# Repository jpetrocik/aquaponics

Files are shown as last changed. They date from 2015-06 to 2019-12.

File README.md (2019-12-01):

# Aquaponic's Firmware For Sonoff Dual R2

Firmware to control an aquaponics system using Sonoff Dual R2.  The Sonoff Dual R2 has two relays to control the pumps, the firmware acts as a timer to control the rely and provides a RestApi to control the pumps from OpenHab or HomeAssistant. The Sonoff curcuit board is removed from the orginal Sonoff enclosure and put into a weather proof enclosure ordered from Amazon.

### Sonoff Dual R2

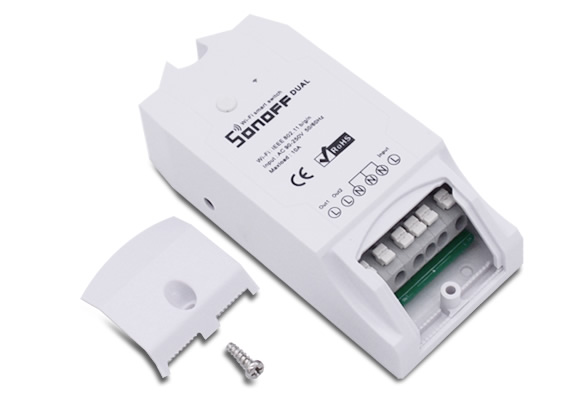
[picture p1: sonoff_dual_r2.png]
Dual R2


## Flashing Firmware

The Sonoff uses a ESP8266 Wifi chip, so this section discusses flashing the ESP8266 chip on the Sonoff Dual R2. For more details google: "Arduino ESP8266"

### Setup the Arduino IDE

* Download Arduino IDE.

* Open you IDE and click on "File -> Preferences".

* In  "Aditional Boards Manager URLs" add this line and click on "OK": "http://arduino.esp8266.com/stable/package_esp8266com_index.json"

* Go to "Tools -> Board -> Boards Manager", type "ESP8266" and install it.

* Go again to "Tools -> Board" and select "Generic ESP8266 Module".

### Flashing

* Place a jumper on the pins labeled BUTTON 0 and GND, without this the Sonoff does not enter flash mode.

* Connect the TTL programmer to programming header pins on the Sonoff.  You must cross over the RX->TX and TX-RX.  So from the promgrammer connect TX -> RX on the Sonoff and RX to TX on the Sonoff.  Connect 3.3v and GND.

* Plug in the programmer your computer.

* Using Adruino IDE, open "firmware.ino" from this project.

* From the menu: Tool -> Boards -> "Generic ESP8266 Module"

* After selecting the board change the following defaults from the Tool menu:

Flash Mode: DOUT (compatiable)

Flash Size: 1M (no spiff)

Port: \<select your programmer from the list\>

* Programming the Sonoff by clickign to "Upload" icon

## Sonoff Dual R2 Programming Headers 

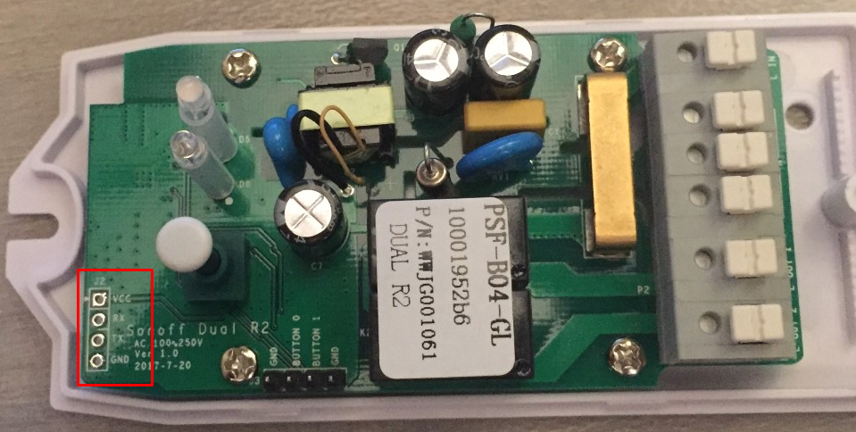
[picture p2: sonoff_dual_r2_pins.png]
Dual R2 Programming Headers


## Enclosure

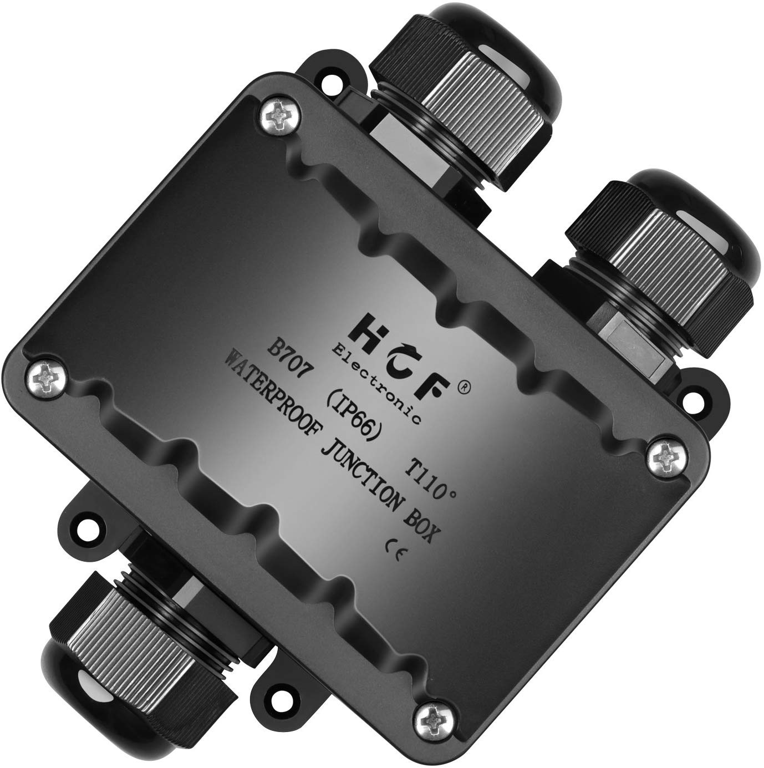
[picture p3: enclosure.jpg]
Enclosure


## Programmer

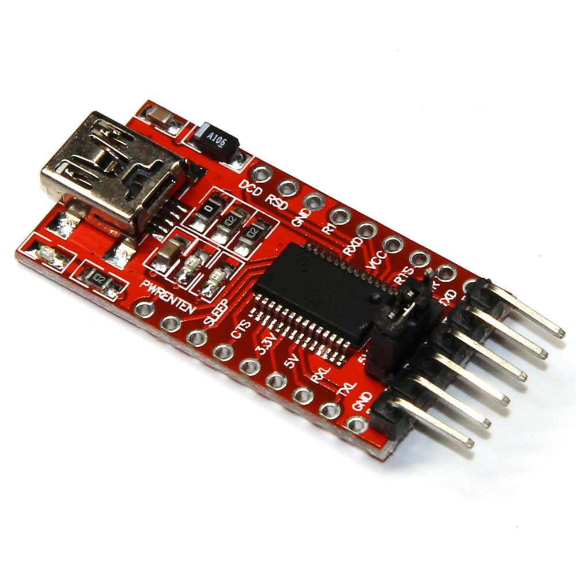
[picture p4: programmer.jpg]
Programmer


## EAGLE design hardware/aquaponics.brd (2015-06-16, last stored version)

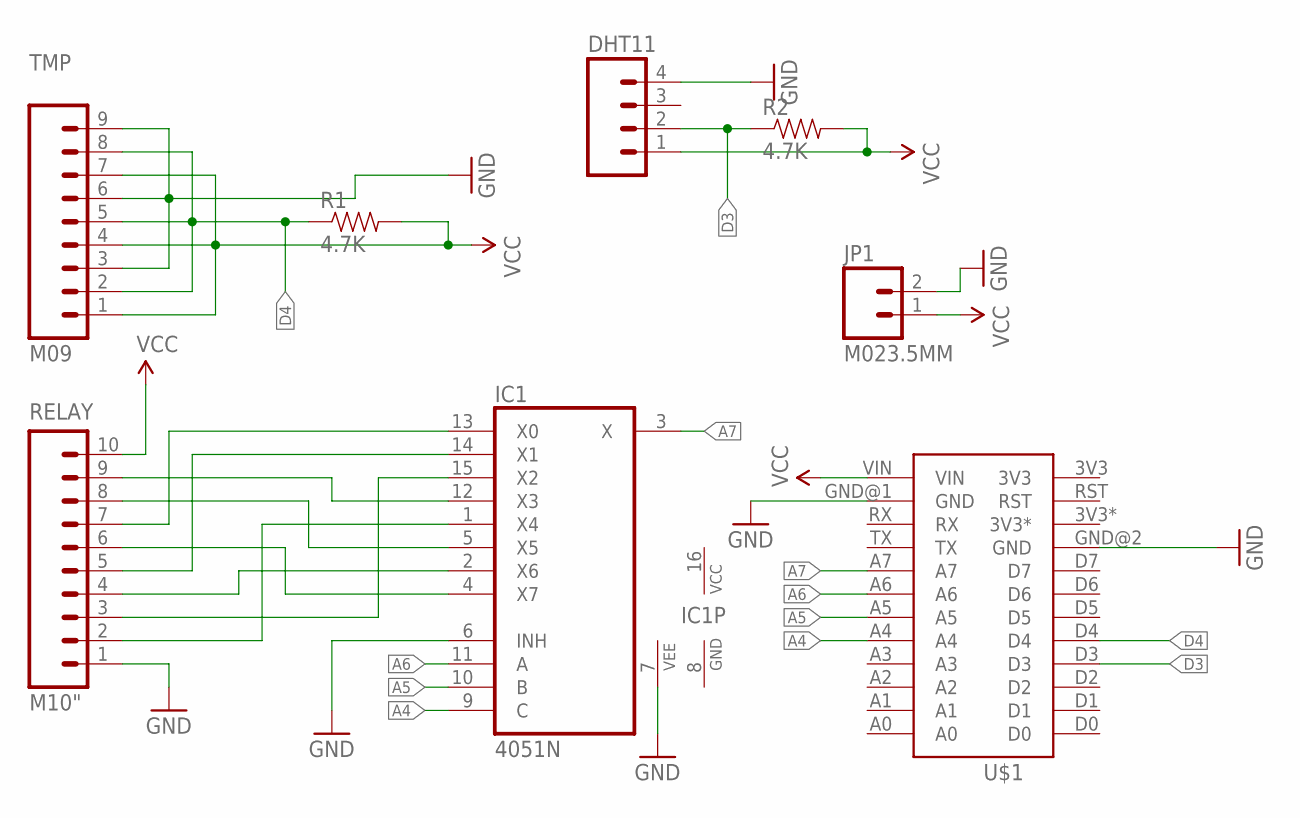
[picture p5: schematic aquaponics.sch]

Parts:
DHT11: M04PTH; 1X04
IC1: 4051N; DIL16
JP1: M023.5MM; SCREWTERMINAL-3.5MM-2
R1, R2: 4.7K; 1206
RELAY: M10"; 1X10
TMP: M09; 1X09
U$1: SPARKCORE

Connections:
A4: IC1.9 (C), U$1.A4
A5: IC1.10 (B), U$1.A5
A6: IC1.11 (A), U$1.A6
A7: IC1.3 (X), U$1.A7
D3: DHT11.2, R2.1, U$1.D3
D4: R1.1, TMP.2, TMP.5, TMP.8, U$1.D4
GND: DHT11.4, IC1.6 (INH), IC1.7 (VEE), IC1.8 (GND), JP1.2, RELAY.1, TMP.3, TMP.6, TMP.9, U$1.GND@1 (GND), U$1.GND@2 (GND)
unnamed: IC1.4 (X7), RELAY.6
unnamed: IC1.2 (X6), RELAY.4
unnamed: IC1.15 (X2), RELAY.3
unnamed: IC1.1 (X4), RELAY.2
unnamed: IC1.14 (X1), RELAY.5
unnamed: IC1.13 (X0), RELAY.7
unnamed: IC1.5 (X5), RELAY.8
unnamed: IC1.12 (X3), RELAY.9
VCC: DHT11.1, IC1.16 (VCC), JP1.1, R1.2, R2.2, RELAY.10, TMP.1, TMP.4, TMP.7, U$1.VIN

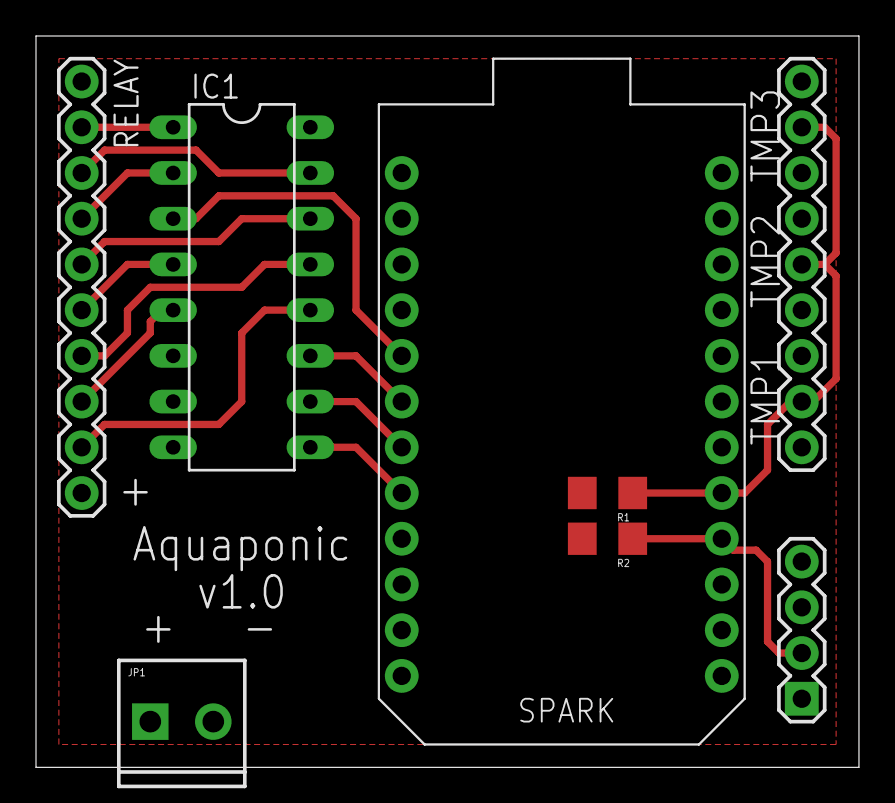
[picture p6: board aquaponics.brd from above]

Board: 2 copper layers, 45.7 x 40.6 mm, 8 parts (0 on the bottom side), 16 nets.

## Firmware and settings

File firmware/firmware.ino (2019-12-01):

#include <ESP8266WiFi.h>

#include <ArduinoOTA.h>
#include <DNSServer.h>
#include <WiFiManager.h>
#include <Ticker.h>
#include <ESP8266mDNS.h>

#include "pump.h"
#include "timer.h"

//configuration
#define BUTTON_0 0
#define RELAY_2 5
#define BUTTON_1 9
#define CASE_SWITCH 10
#define RELAY_1 12
#define LED_BLUE 13

//Control variables
int remainingTime = 0;
int nextStart = 0;
int pumpStatus = 0;
bool shouldAccessPointConfig = false;

char hostname[41] = "aquaponics";

Ticker ticker;

Pump pump(RELAY_1);
PumpTimer timer;

void setup()
{

  Serial.begin(115200);

  Serial.println("Aquaponics Firmware");
  Serial.println(__DATE__ " " __TIME__);
  Serial.println(hostname);

  pinMode(LED_BLUE, OUTPUT);

  ticker.attach(0.6, tick);

  wifiSetup();

  mdnsSetup();

  ticker.detach();
  
  otaSetup();

  webServerSetup();

  timer.control(&pump, 15 * 60 * 1000, 45 * 60 * 1000);

  digitalWrite(LED_BLUE, !false);

}

void startPump() {
  pumpStatus = pump.start();
}

void stopPump() {
  pumpStatus = pump.stop();
}

void loop()
{
  timer.update();
  pump.update();

  remainingTime = timer.remainingTime();
  nextStart = timer.nextStart();
  pumpStatus = (int)pump.status();

  
  otaLoop();

  webServerLoop();

}

void factoryReset() {
  Serial.println("Restoring Factory Setting....");
  WiFi.disconnect();
  //SPIFFS.format();
  delay(500);
  Serial.println("Restarting....");
  ESP.restart();
}

void tick() {
  int state = digitalRead(LED_BLUE);
  digitalWrite(LED_BLUE, !state);
}

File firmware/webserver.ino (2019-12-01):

ESP8266WebServer server(80); 


void webServerSetup() {
  Serial.println("Starting web server on port 80");
   server.on("/", handleStatus); 
   server.on("/pump/on", handleStartPump); 
   server.on("/pump/off", handleStopPump); 
   server.on("/restart", HTTP_POST, handleRestart); 
   server.on("/factoryreset", HTTP_POST, handleFactoryReset); 
   
   server.begin();
}

void webServerLoop() {
  server.handleClient();
}

void handleStartPump() {
  startPump();
  handleStatus();
}

void handleStopPump() {
  stopPump();
  handleStatus();
}

void handleStatus() {
  char jsonStatusMsg[140];
  
  sprintf (jsonStatusMsg, "{\"pump\":%s,\"timer\":\"%i\",\"next\":\"%i\"}", pumpStatus ? "\"ON\"" : "\"OFF\"", remainingTime>0?remainingTime:0, nextStart);
  server.send(200, "application/json",  (char *)jsonStatusMsg);
}

void handleRestart() {
  server.send(200, "application/json",  "{\"message\":\"Restarting\"}");
  delay(1000);
  ESP.restart();
}

void handleFactoryReset() {
  factoryReset();
  delay(1000);
  server.send(200, "application/json",  "{\"message\":\"Factory Reset\"}");
}

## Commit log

2015-06-16 Added heater monitor
2015-06-16 Move firmware files to firmware and added eagle pcb files
    [aquaponics.brd, aquaponics.sch]
2016-01-11 Upgraded OneWire and resolved Timer name conflict
2018-06-12 Added start/stop pump api call
2019-12-01 Moved to Sonoff Dual R2 hardware
    [aquaponics.brd, aquaponics.sch]
2019-12-01 Adding enclosure image
2019-12-01 Fixed enclosure image link

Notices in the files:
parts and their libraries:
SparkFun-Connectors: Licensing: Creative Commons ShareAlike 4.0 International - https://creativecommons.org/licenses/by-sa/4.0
